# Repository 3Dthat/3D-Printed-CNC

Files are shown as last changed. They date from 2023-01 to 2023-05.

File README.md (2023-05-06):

# 3D Printed CNC
This is a 3D Printable CNC machine. I am still working on adding all the wiring, cable chains and endstops.

This is 1500mm x 1000mm. At this size the cost is around $1300. If you make it smaller the cost goes down a lot.

Full Open Source for anyone to use.

You can scale the size by changing the length of the Extrusions, Linear Rails and Ball Screws to the size you want. All the 3D Printed parts will be the same.

Fusion 360 CAD File: https://drive.google.com/file/d/1byu-iDm4qr-0gbzB1d7eL87Z1ogVPFDh

STEP Cad File: https://drive.google.com/file/d/1XpXRZY43732uwQITwHpzu3FDPc9UsANn

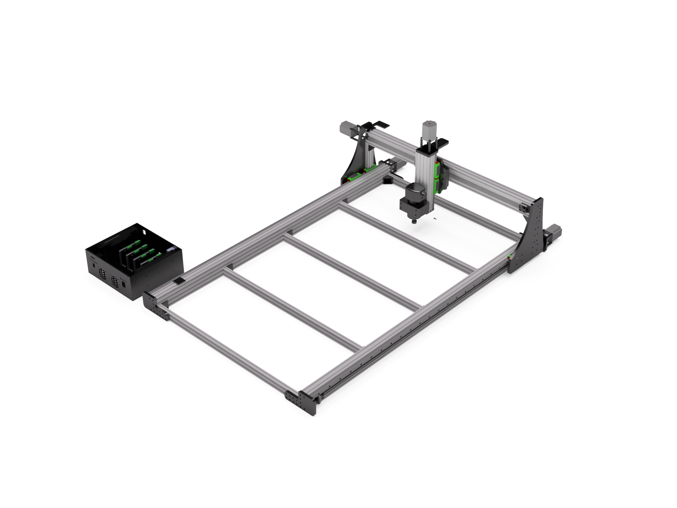
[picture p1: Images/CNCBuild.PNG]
3dthat 3d Printed CNC


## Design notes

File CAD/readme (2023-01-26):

CAD files for the 3D printed CNC machine.

I will get my Fusion 360 file uploaded soon. Right now the file size is to big.

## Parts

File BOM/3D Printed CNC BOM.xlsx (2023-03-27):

Type | Component | QTY | Source
Printed Parts |  |  | Print Yourself or Buy Here (http://3dthat.com/)
Frame | 2040 Inside Corner | 12 | Amazon (https://www.amazon.com/Iverntech-Aluminum-Extrusion-Brackets-Connector/dp/B0B56VNRGG?th=1)
 | 2040 Extrusion 860mm | 5 | Amazon (https://www.amazon.com/dp/B09JG61217)
 | 2040 Extrusion 138mm | 2
 | C Beam Extrusion 1500mm | 2 | OpenBuilds (https://openbuildspartstore.com/c-beam-linear-rail/)
 | C Beam Extrusion 1000mm | 1 | OpenBuilds (https://openbuildspartstore.com/c-beam-linear-rail/)
 | C Beam Extrusion 300mm | 1 | OpenBuilds (https://openbuildspartstore.com/c-beam-linear-rail/)
Motion | SFU 1204 Ball Screw 1500mm | 2 | Ebay (https://www.ebay.com/itm/165367993854)
 | SFU 1204 Ball Screw 1000mm | 1
 | SFU 1204 Ball Screw 350mm | 1
 | FK10 & FF10 End Support | 4 | Amazon (https://www.amazon.com/gp/product/B08NPFBH9F) | Use Bearing out of FF12
 | Motor Shaft Coupler | 4 | Amazon (https://www.amazon.com/dp/B078VR9V7J)
 | HGR20 Linear Rail 1500mm | 2 | Amazon (https://www.amazon.com/dp/B08HCQFGTK)
 | HGR20 Linear Rail 1000mm | 2
 | HGR20 Linear Rail 300mm | 2
Electronics | Nema 23 Stepper Motor | 4 | Amazon (https://www.amazon.com/dp/B00PNEPW4C)
 | Stepper Driver DM556 Nema 23 | 4 | Amazon (https://www.amazon.com/dp/B08J3NFF9V)
 | 24v Power Supply | 1 | Amazon (https://www.amazon.com/dp/B07YYCXV5S)
 | ESP 32 | 1 | Amazon (https://www.amazon.com/HiLetgo-ESP-WROOM-32-Development-Microcontroller-Integrated/dp/B0718T232Z)
Fasteners | M5x12 Button Head | 190 | Amazon (https://www.amazon.com/dp/B07NVCHPKR)
 | M5x16 Button Head | 112
 | M5x20 Button Head | 6
 | M5x30 Button Head | 12
 | M5x50 Button Head | 4 | Amazon (https://www.amazon.com/dp/B01D9JE0JU)
 | M5x70 Socket Head | 16 | Amazon (https://www.amazon.com/dp/B089Q76WZW)
 | M5x80 Socket Head | 8 | Amazon
 | M4x12 Button Head | 32 | Amazon (https://www.amazon.com/dp/B0975MW8BT)
 | M4x16 Button Head | 12
 | M5 T-Nut | 166 | Amazon (https://www.amazon.com/Fastener-Nickel-Plated-Sliding-Aluminum-Profile/dp/B086MKNYDS)
 | M4 Threaded Insert | 40 | Amazon (https://www.amazon.com/dp/B08T9TXS9S)
 | M5 Threaded Insert | 38 | Amazon (https://www.amazon.com/dp/B07YSVXWS8)

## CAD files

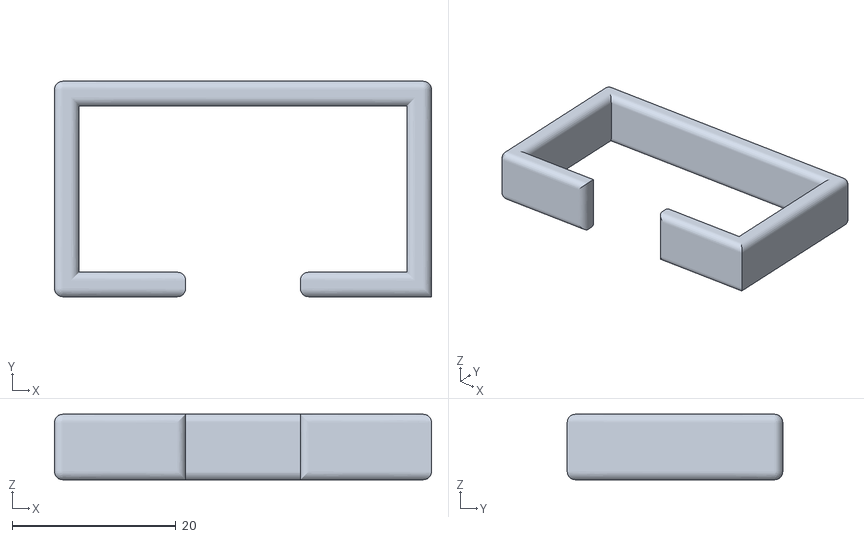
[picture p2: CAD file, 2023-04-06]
STLs/Drag-Chain/Fixed_drag_chain_clip.stl
46.0 x 26.3 x 8.00

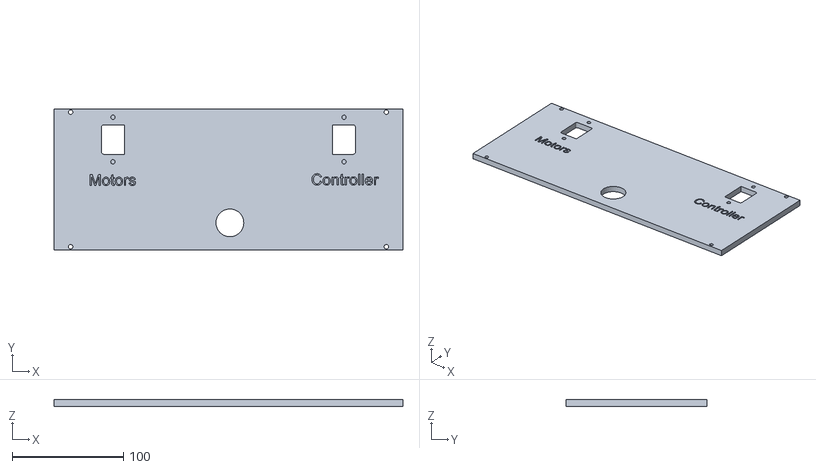
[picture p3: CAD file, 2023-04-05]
STLs/Electronics_Enclosure/Back.stl
314.0 x 127.0 x 6.00

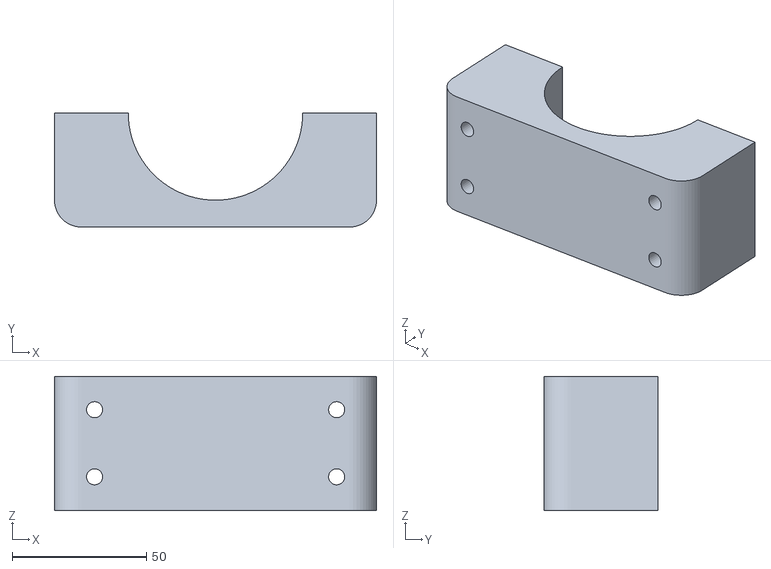
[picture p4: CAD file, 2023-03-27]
STLs/Router-Mounts/Makita_Mount_Front.stl
120.0 x 42.5 x 50.0

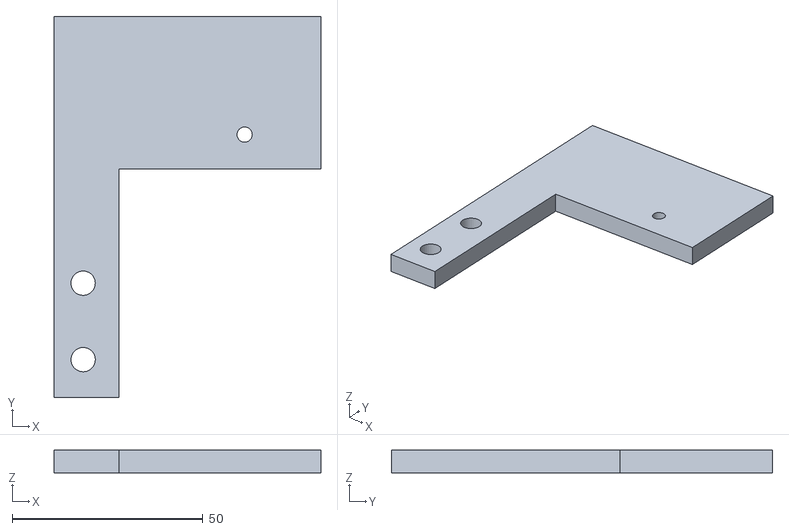
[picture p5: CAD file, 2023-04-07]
STLs/X-Axis/Y_Chain_Top_Support.stl
70.0 x 100.0 x 6.00

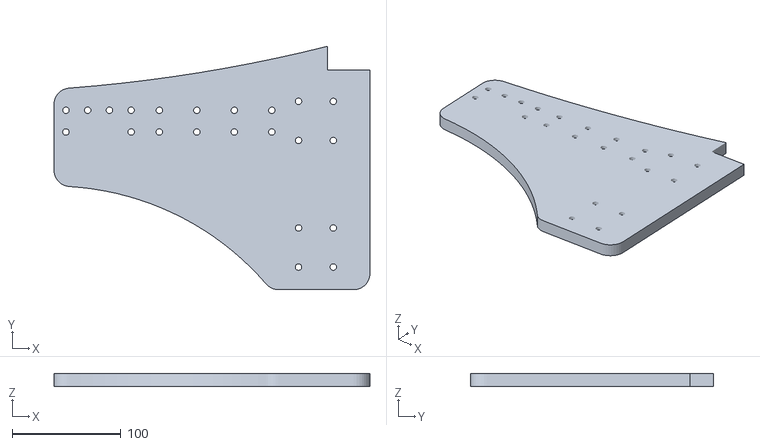
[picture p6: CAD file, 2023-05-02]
STLs/Y-Axis/XY Connector Plate Right.stl
290.8 x 224.0 x 12.0

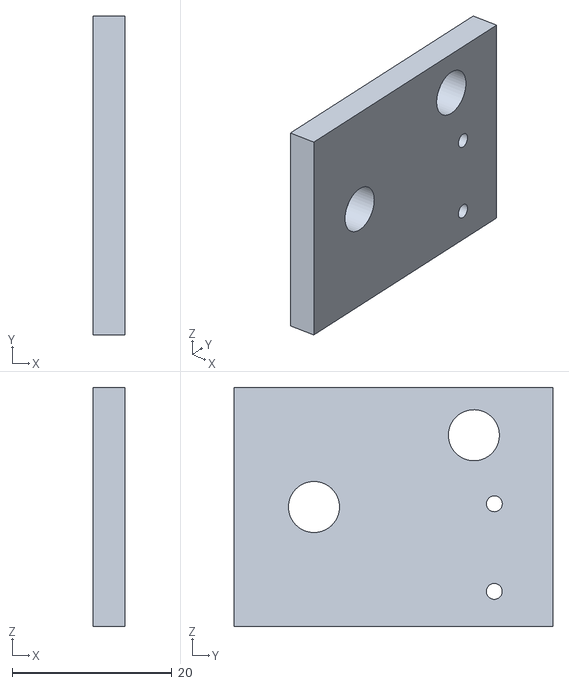
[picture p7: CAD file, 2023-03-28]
STLs/Z-Axis/Z_Enstop_Mount.stl
4.00 x 40.0 x 30.0

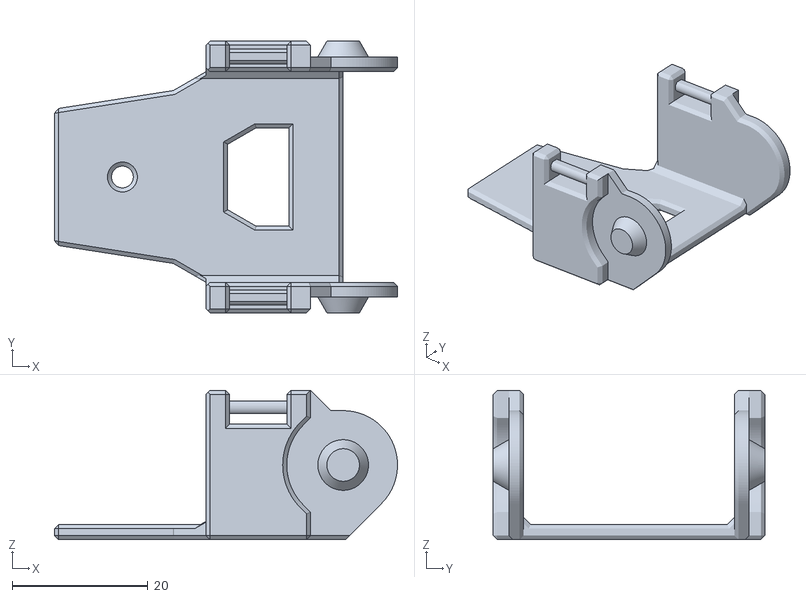
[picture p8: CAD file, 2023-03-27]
STLs/Drag-Chain/drag_chain_end_male.STL
50.5 x 40.0 x 22.0

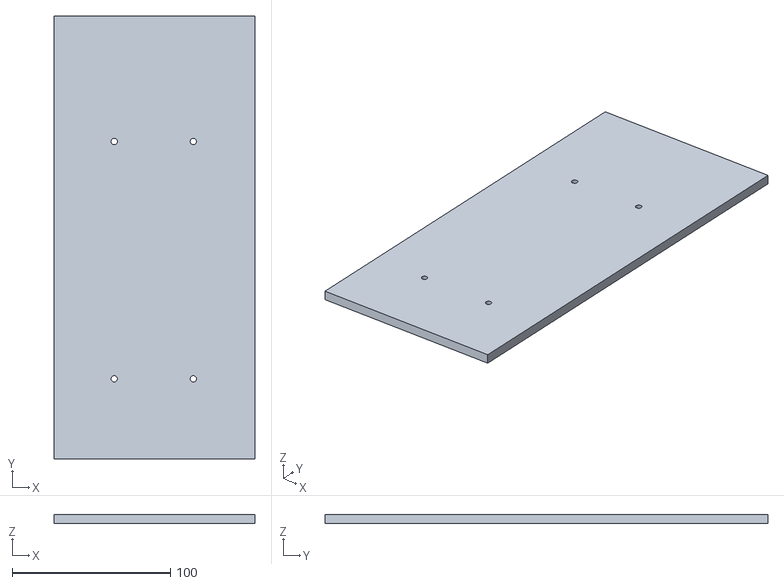
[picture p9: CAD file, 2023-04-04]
STLs/Electronics_Enclosure/Left.stl
127.0 x 280.0 x 6.00

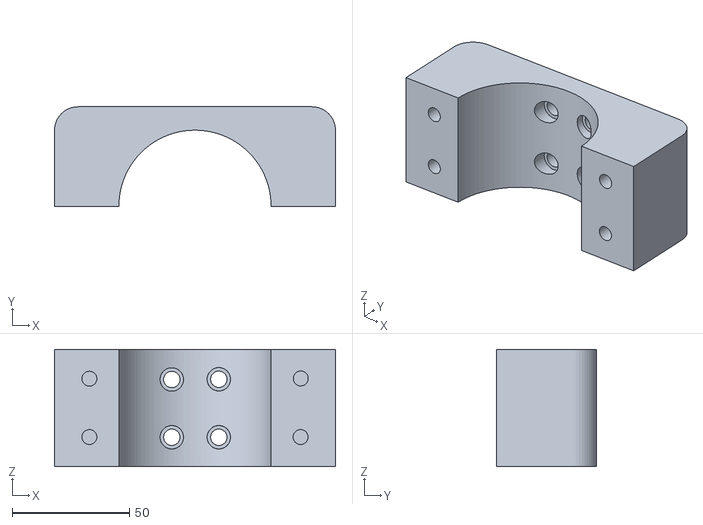
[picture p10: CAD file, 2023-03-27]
STLs/Router-Mounts/Makita_Mount_Back.stl
120.0 x 42.5 x 50.0

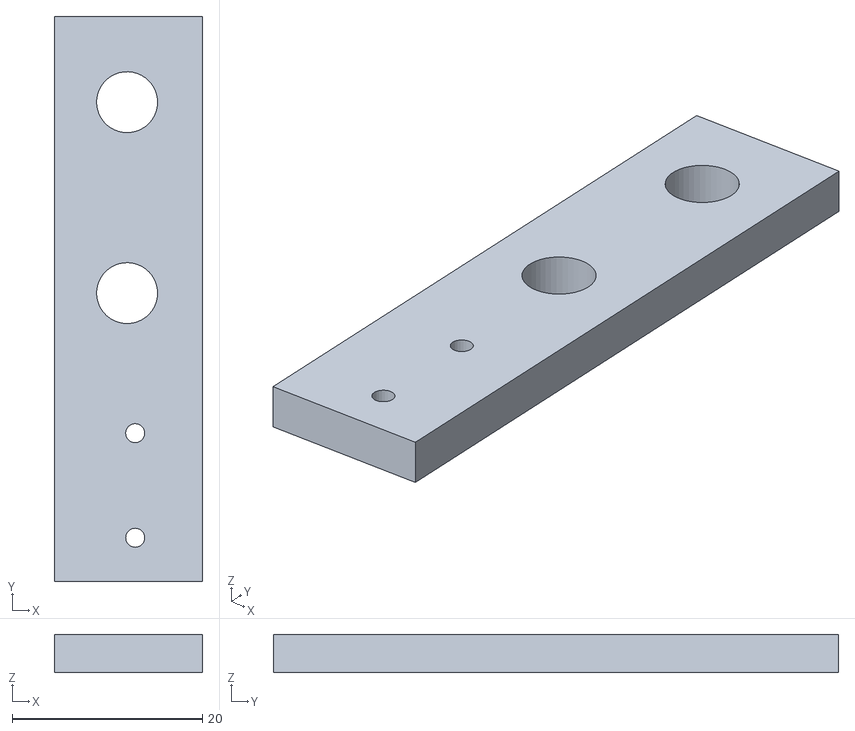
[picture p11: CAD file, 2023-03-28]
STLs/X-Axis/X_Endstop_Mount.stl
15.6 x 59.3 x 4.00

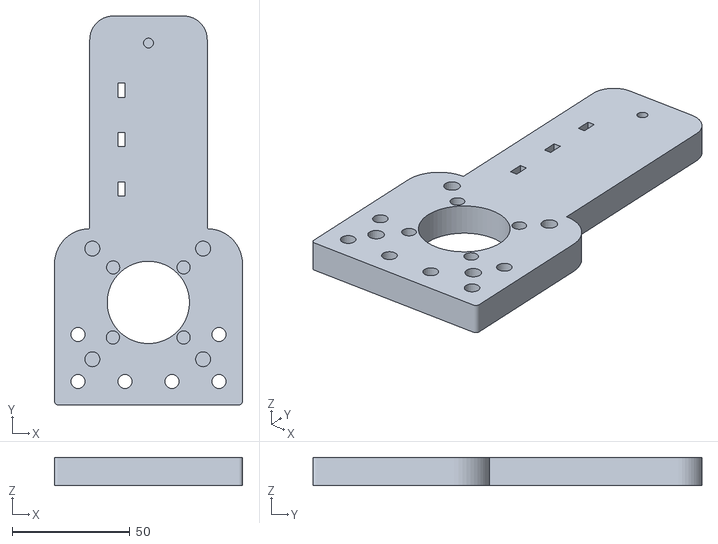
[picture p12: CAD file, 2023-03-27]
STLs/Z-Axis/Top_Plate.stl
80.0 x 165.5 x 12.0

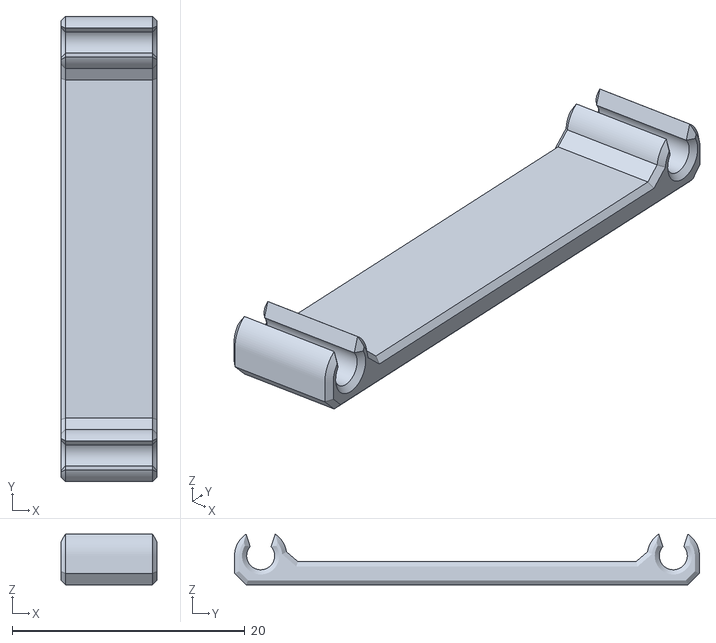
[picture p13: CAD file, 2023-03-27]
STLs/Drag-Chain/drag_chain_clip.STL
8.30 x 40.0 x 4.37

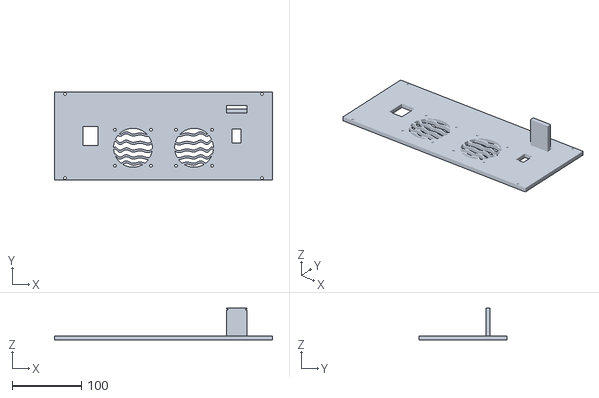
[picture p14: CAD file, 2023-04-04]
STLs/Electronics_Enclosure/Front.stl
314.0 x 127.0 x 46.0

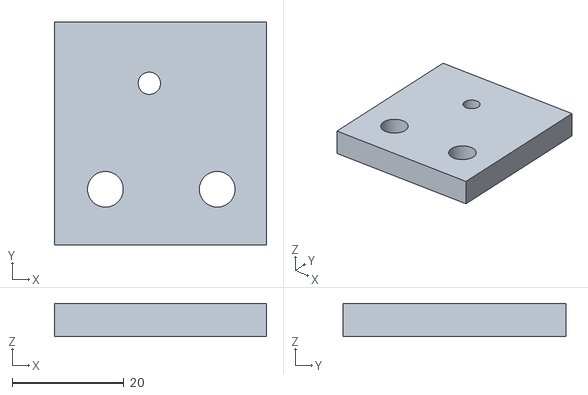
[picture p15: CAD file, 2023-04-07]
STLs/Y-Axis/Y_Chain_Bottom_Mount.stl
38.0 x 40.0 x 6.00

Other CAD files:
STLs/Y-Axis/XY Connector Plate Left.stl
STLs/Z-Axis/Z_Motor_Spacer_x4.stl
STLs/Drag-Chain/drag_chain_end_female.STL
STLs/Electronics_Enclosure/Top.stl
STLs/Drag-Chain/drag_chain_link.STL
STLs/Electronics_Enclosure/Bottom.stl
STLs/Electronics_Enclosure/Right.stl
STLs/X-Axis/BallScrew Connector.stl
STLs/X-Axis/X Plate.stl
STLs/X-Axis/X_BallScrew_End_Bearing.stl
STLs/Y-Axis/Back_Plat_Left.stl
STLs/Y-Axis/Back_Plate_Right.stl
STLs/Y-Axis/BallScrew Connector Left.stl
STLs/Y-Axis/BallScrew Connector Right.stl
STLs/Y-Axis/Front Connector Plate Left.stl
STLs/Y-Axis/Front Connector Plate Right.stl
STLs/Y-Axis/Y_BallScrew_End_Bearing_Left.stl
STLs/Y-Axis/Y_BallScrew_End_Bearing_Right.stl
STLs/Y-Axis/Y_Endstop_Mount_x2.stl
STLs/Y-Axis/Y_Motor_Spacer_x8.stl
STLs/Z-Axis/BallScrew Connector.stl
STLs/Z-Axis/Bottom_Plate.stl
STLs/Z-Axis/Z Plate.stl

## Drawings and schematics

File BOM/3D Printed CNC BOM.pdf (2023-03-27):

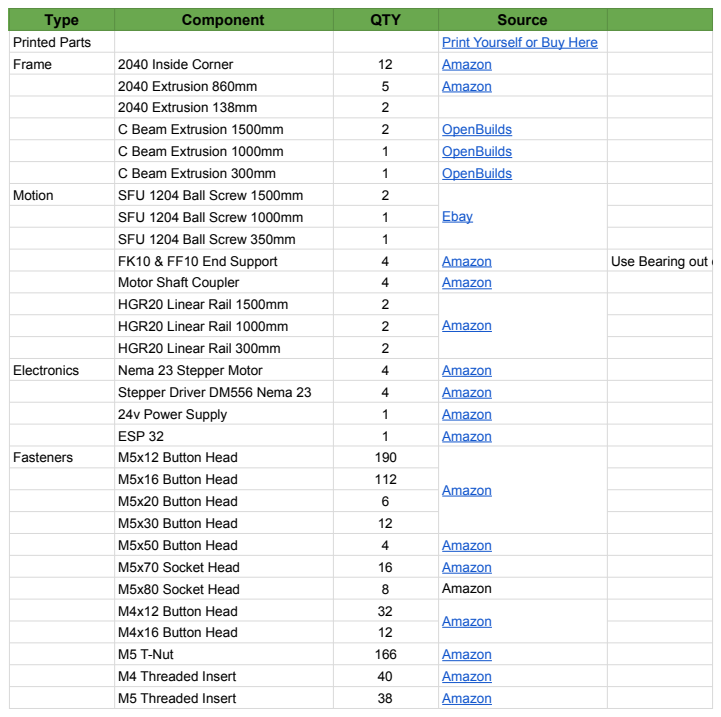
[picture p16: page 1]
Type; Component; QTY; Source; Printed Parts; Print Yourself or Buy Here; Frame; 2040 Inside Corner; Amazon; 2040 Extrusion 860mm; 2040 Extrusion 138mm; C Beam Extrusion 1500mm; OpenBuilds; C Beam Extrusion 1000mm; C Beam Extrusion 300mm; Motion; SFU 1204 Ball Screw 1500mm; SFU 1204 Ball Screw 1000mm; Ebay; SFU 1204 Ball Screw 350mm; FK10 & FF10 End Support; Use Bearing out of FF12; Motor Shaft Coupler; HGR20 Linear Rail 1500mm; HGR20 Linear Rail 1000mm; HGR20 Linear Rail 300mm; Electronics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

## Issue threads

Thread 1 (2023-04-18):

Laser diode

maframan, 2023-04-18:
Hi, thanks for your beatiful project.
In your project is it possible to mount laser diode? If yes, how do i do?
Can you share the BOM for mount laser diode?

Thanks a lot for your support

3Dthat, 2023-04-22:
Hi,

Yes of course you can mount a laser to it.

Send me a link to the laser you want to attach and I can make a mount for it. :)

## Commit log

2023-01-25 Create CAD
2023-01-25 Update CAD
2023-02-07 Changed M5 Mounting Hole Size
    Bigger M5 hole size for easier installation.
    [Bottom Plate.stl]
2023-02-07 Changed M5 Holes for easy install.
    [Top_Plate.stl]
2023-02-07 Changed M5 hole size for easier install.
    [Back Connector Plate Left.stl, Back Connector Plate Right.stl, Front Connector Plate Left.stl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]
2023-03-26 Updated Bearing Hole Size
    [Y_BallScrew_End_Bearing_Left.stl, Y_BallScrew_End_Bearing_Right.stl]
2023-03-26 Fixed Screw Holes
    [Back_Plat_Left.stl, Back_Plate_Right.stl]
2023-03-26 Fixed Bearing Hole Size
    [X_BallScrew_End_Bearing.stl]
2023-03-27 Made Mount Bigger and Stronger
    [Makita_Mount_Back.stl, Makita_Mount_Front.stl]
2023-03-27 Added Drag Chain Mount
    [Top_Plate.stl]
2023-05-02 Changed Top Height to save on filament.
    [XY Connector Plate Left.stl, XY Connector Plate Right.stl]
